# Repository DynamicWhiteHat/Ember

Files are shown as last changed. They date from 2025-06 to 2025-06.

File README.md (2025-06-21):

# Ember
## A Custom Designed 10W Diode Laser Cutter

## IMPORTANT: It is imperative to ensure proper safety when operating, observing, or in the vicinity of a powerful laser. Please ensure you have proper PPE equipment and handle lasers safely. Please see the BOM for a recommended pair of PPE.

### Specifications:

- NEJE E40 10W 24v Diode Laser
- Wireless connectivity powered by the MakerBase DLC32 board
- TS35 touchscreen
- 400x400 mm total area → 360x360 mm cutting area
- 2x endstops for auto homing
- Dual-driven y-axis
- Emergency Stop

### Why I Designed This Project

I wanted to design a low-cost, yet powerful, laser cutter with ample build space. After looking at [this](https://www.youtube.com/watch?v=NyUJvcocJpA) YouTube video, I realized that laser cutters are relatively simple to build. This was also my first time designing something major with moving and press-fit parts in Fusion 360, so it was also a learning experience.
I ensured that I included more than just the necessary elements by adding features such as wireless connectivity and touchscreen access. Nonetheless, this project can still be improved, as it could use more precise 0.9° steppers and lacks an air assist system.
Overall, this was a fun yet demanding project that tested my skills in planning, design, and budgeting, and I think I created a good final product.

### Image Gallery





Rough Wiring: 

Untitled presentation

### BOM
NOTE: Without the AliExpress welcome deal (which only applies to the first product I order), most of these products are cheaper from Amazon, which is why many of them are sourced from there.

Recommended PPE (anything OD 6+): https://www.amazon.com/190nm-490nm-Professional-Protective-Wavelength-Protection/dp/B08R4PMCHR 
| Part | Quantity | Price | Link |
|---|---|---|---|
| Laser | 1 | $134.83 | https://neje.shop/products/e40?variant=40316129378440 |
| DLC32+Screen | 1 |  $47.37 | https://www.aliexpress.us/item/3256804976730248.html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 |
| NEMA17 Stepper | 3 |  $25.99 | https://www.amazon.com/STEPPERONLINE-Stepper-Bipolar-42x42x38mm-Connector/dp/B0B38GHRH8/ |
| Endstop | 1 Pack Of 6 (Cheapest) | $9.99 | https://www.amazon.com/REIFENG-Mechanical-Endstop-Horizontal-Ramps1-4/dp/B07PCN6T6F/ |
| 4x 8mm Shaft | 1 Pack Of 4 |  $16.99 | https://www.amazon.com/inches-Vigorous-Linear-Hardened-Printer/dp/B0CXTX5FZ3/ |
| Bed | 1 |  $35.99 | https://www.amazon.com/UniTak3D-Honeycomb-400x400mm-Dissipation-Protection/dp/B0DHH5XBNH/ |
| LM8UU | 1 Pack Of 10 | $7.65 | https://www.aliexpress.us/item/3256806883965670.html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 |
| 4x 2020 Extrusions + Gussets | 1 Pack Of 4 |  $17.99 | https://amazon.com/Aluminum-Extrusion-European-Standard-Anodized/dp/B0CLGYRKS8/ |
| GT2 Pulley + Belt + Idlers | 1 |  $13.99 | https://www.amazon.com/KeeYees-Timing-Tensioner-Torsion-Printer/dp/B07JKT5BZQ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 |
| E-STOP | 1 | $2.00 | https://www.aliexpress.us/item/2255800895415537.html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 |
| PSU | 1 |  $35.99 | https://www.amazon.com/ALITOVE-100-240V-Converter-Transformer-5-5x2-5mm/dp/B0B17Z1V6B/ |
| TOTAL: | | $348.78 | |

Additional parts (out of pocket cost) [screws](https://www.amazon.com/HanTof-Countersunk-Machine-Wrenches-Threaded/dp/B0B9HWVV61/)

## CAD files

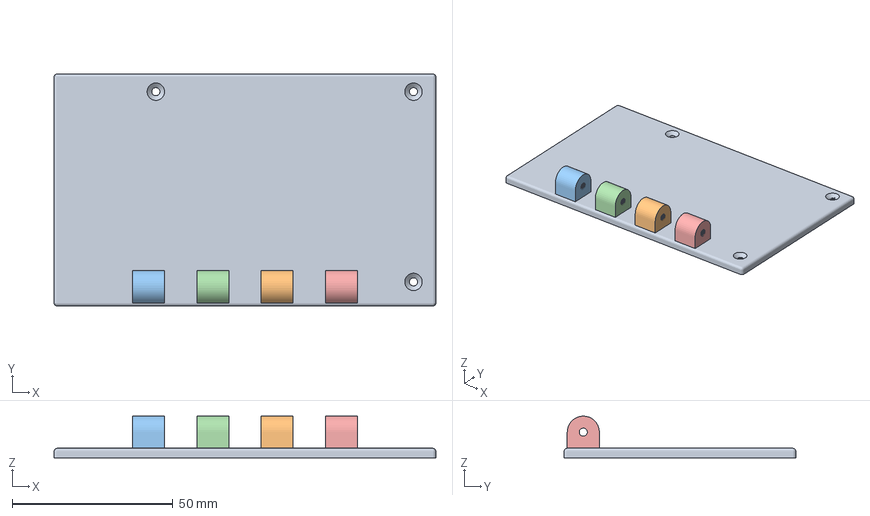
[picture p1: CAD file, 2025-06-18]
CAD/Prints/3MF/MCU/MainTop.3mf
118.9 x 72.2 x 13.0 mm

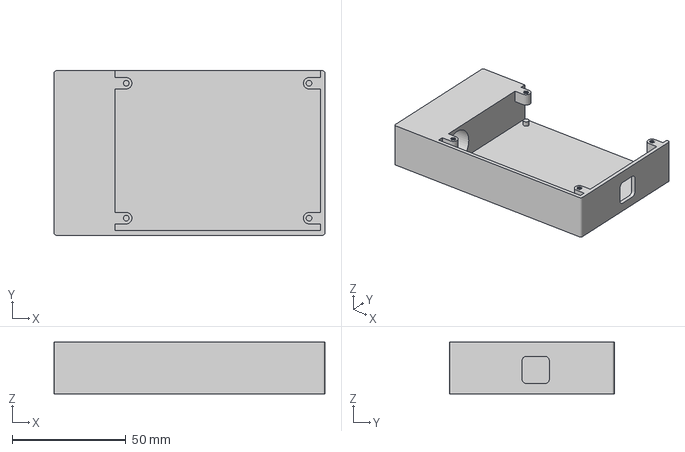
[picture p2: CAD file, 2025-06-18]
CAD/Prints/3MF/MCU/MainBottom.3mf
118.9 x 72.2 x 22.7 mm

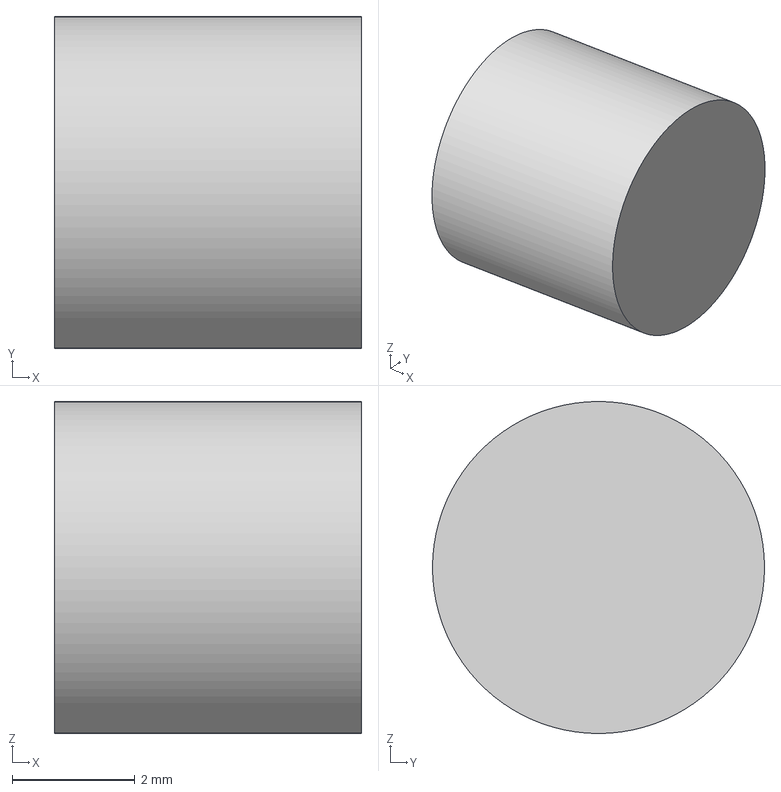
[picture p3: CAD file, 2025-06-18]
CAD/Prints/3MF/Extras/BearingFiller.3mf
5.00 x 5.40 x 5.40 mm

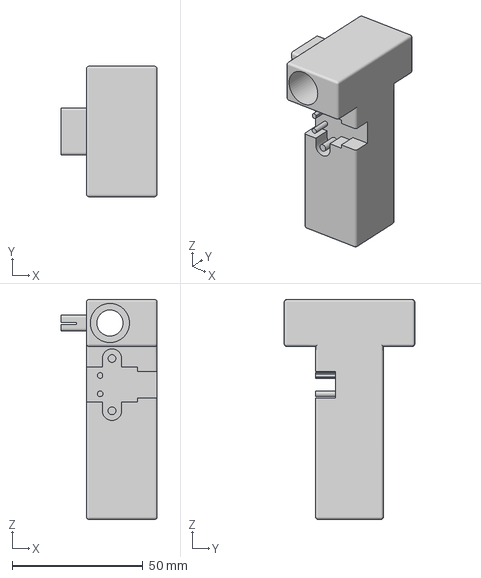
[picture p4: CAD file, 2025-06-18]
CAD/Prints/3MF/Motion/LeftX.3mf
36.9 x 50.0 x 84.2 mm

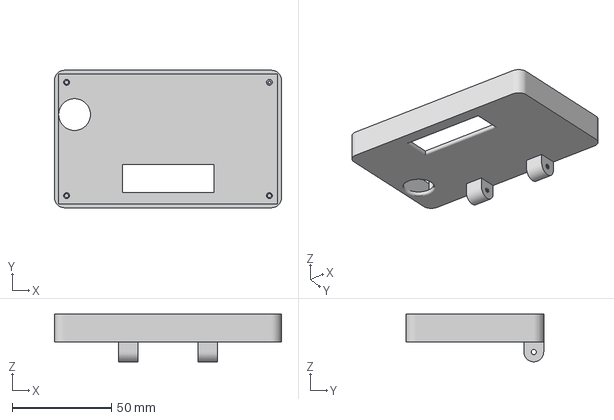
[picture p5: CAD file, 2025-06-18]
CAD/Prints/3MF/Screen/ScreenBottom.3mf
114.2 x 69.2 x 24.0 mm

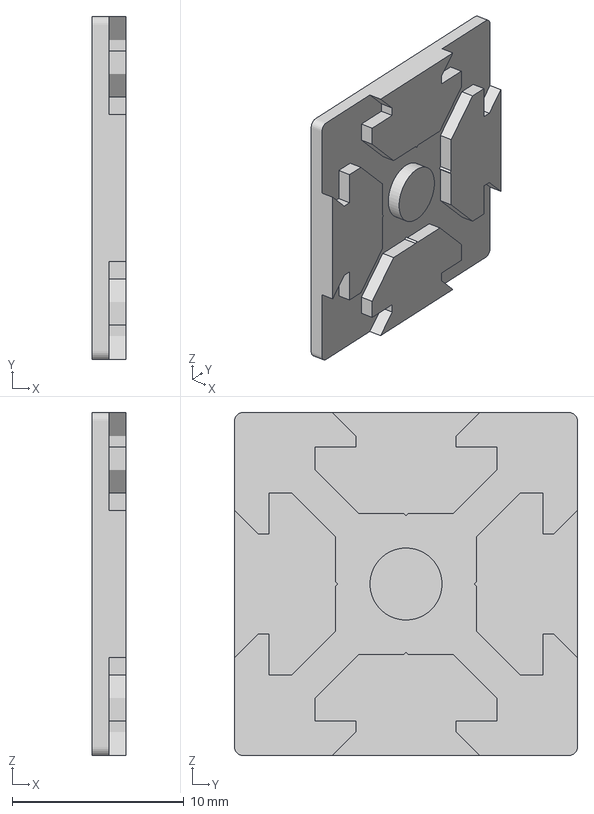
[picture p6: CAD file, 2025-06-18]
CAD/Prints/3MF/Extras/EndCaps2020.3mf
2.00 x 20.0 x 20.0 mm

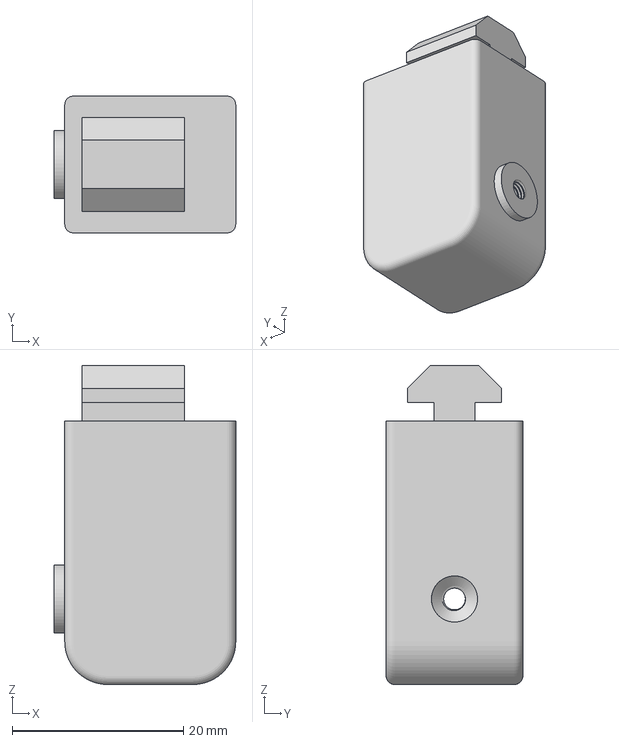
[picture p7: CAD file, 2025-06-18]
CAD/Prints/3MF/Motion/BRightBearing.3mf
21.2 x 16.0 x 37.3 mm

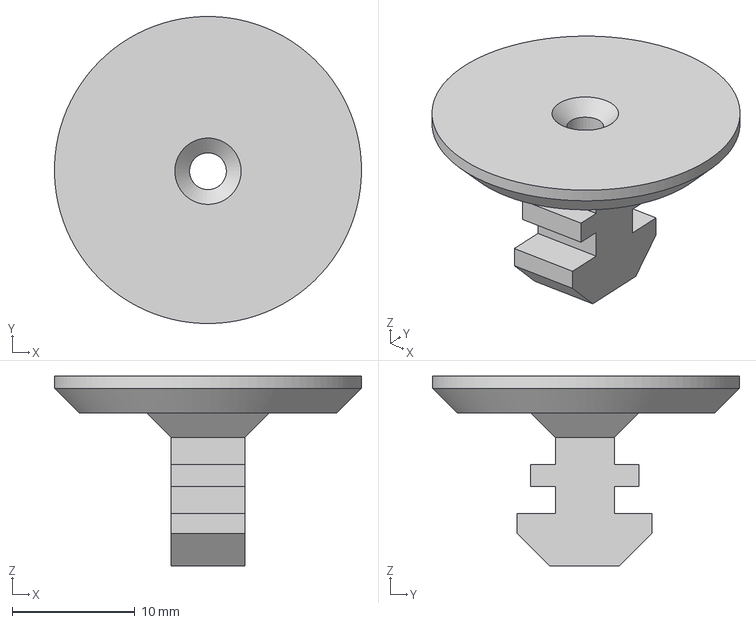
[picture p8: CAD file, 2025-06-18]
CAD/Prints/3MF/Motion/Foot.3mf
25.0 x 25.0 x 15.5 mm

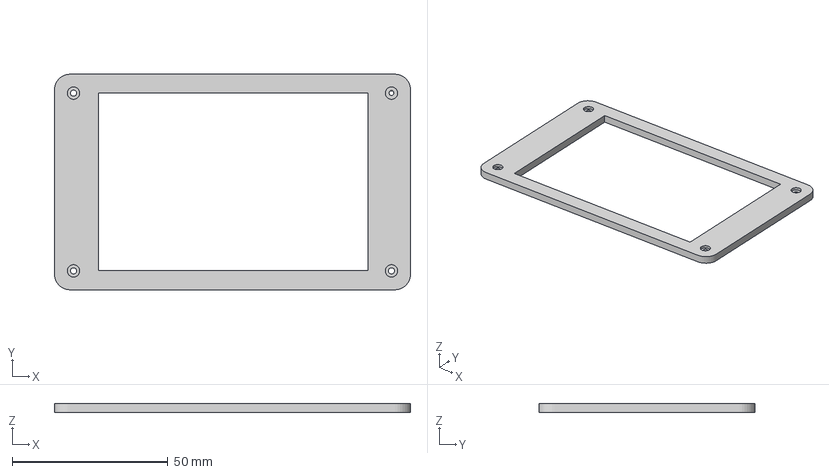
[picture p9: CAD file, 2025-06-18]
CAD/Prints/3MF/Screen/ScreenLid.3mf
114.2 x 69.2 x 2.94 mm

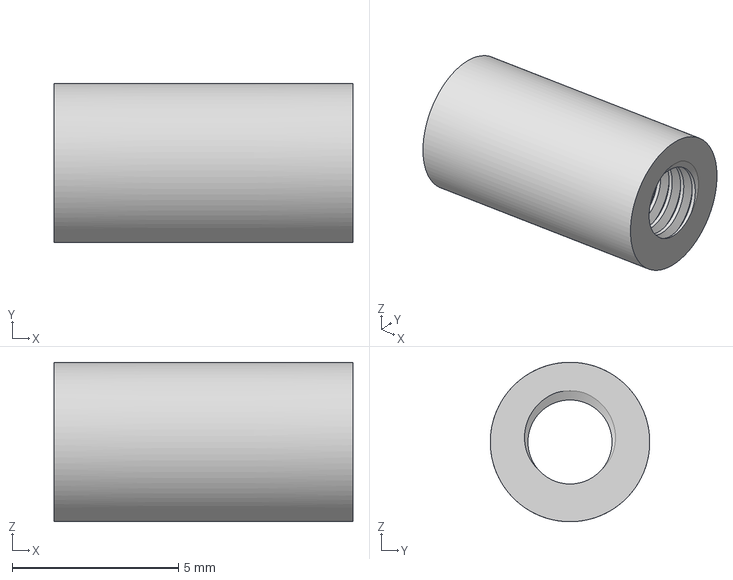
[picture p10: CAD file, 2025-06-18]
CAD/Prints/3MF/Motion/BearingInsertRight.3mf
9.00 x 4.80 x 4.80 mm

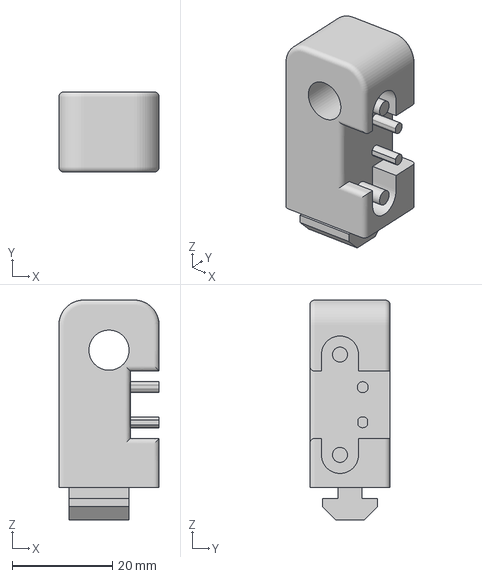
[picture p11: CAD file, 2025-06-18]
CAD/Prints/3MF/Motion/FRight.3mf
20.0 x 16.0 x 43.8 mm

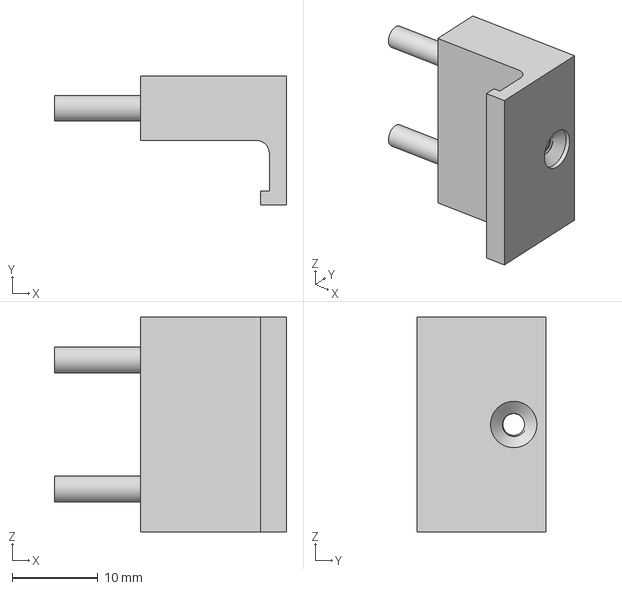
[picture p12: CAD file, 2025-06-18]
CAD/Prints/3MF/Motion/ZHolder1.3mf
27.0 x 15.0 x 25.0 mm

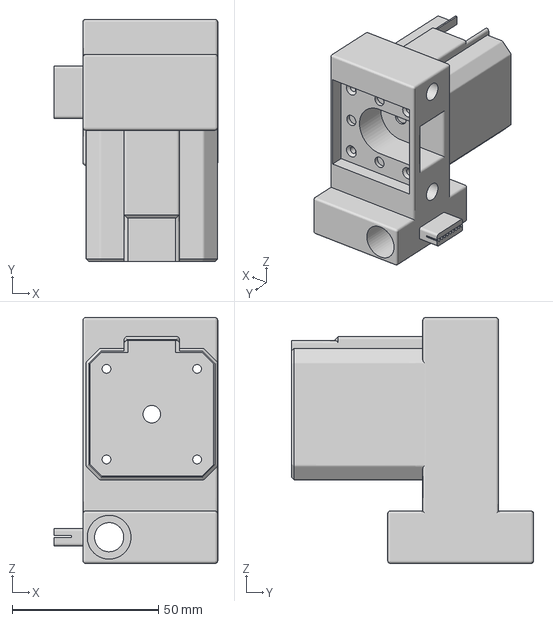
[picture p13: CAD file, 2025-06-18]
CAD/Prints/3MF/Motion/RightX.3mf
56.0 x 83.0 x 84.2 mm

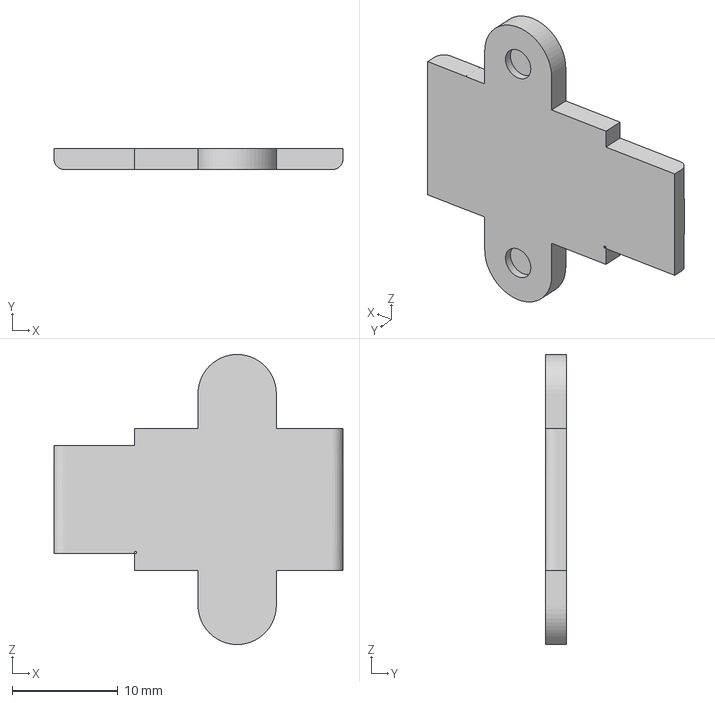
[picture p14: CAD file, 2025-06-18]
CAD/Prints/3MF/Motion/LeftMagnet.3mf
27.3 x 2.00 x 27.4 mm

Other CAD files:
CAD/Prints/3MF/Motion/BLeftBearing.3mf
CAD/Prints/3MF/Motion/BearingInsertLeftX.3mf
CAD/Prints/3MF/Motion/Holder.3mf
CAD/Prints/3MF/Motion/Magnetic.3mf
CAD/Prints/3MF/Motion/BLeft.3mf
CAD/Prints/3MF/Motion/BRight.3mf
CAD/Prints/3MF/Motion/BearingInsertLeft.3mf
CAD/Prints/3MF/Motion/FLeft.3mf
CAD/Prints/3MF/Motion/ZHolder2.3mf
CAD/Prints/3MF/Screen/ScreenScrew.3mf
CAD/Prints/STL/Extras/BearingFiller.stl
CAD/Prints/STL/Extras/EndCaps2020.stl
CAD/Prints/STL/MCU/MainBottom.stl
CAD/Prints/STL/MCU/MainTop.stl
CAD/Prints/STL/Motion/BLeft.stl
CAD/Prints/STL/Motion/BLeftBearing.stl
CAD/Prints/STL/Motion/BRight.stl
CAD/Prints/STL/Motion/BRightBearing.stl
CAD/Prints/STL/Motion/BearingInsertLeft.stl
CAD/Prints/STL/Motion/BearingInsertLeftX.stl
CAD/Prints/STL/Motion/BearingInsertRight.stl
CAD/Prints/STL/Motion/FLeft.stl
CAD/Prints/STL/Motion/FRight.stl
CAD/Prints/STL/Motion/Foot.stl
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

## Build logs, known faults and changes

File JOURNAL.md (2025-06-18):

# Ember
A Custom Built 10w Laser Cutter

---
title: "Ember"
author: "DynamicWhiteHat"
description: "A custom-built $350 10w laser cutter."
created_at: "2025-06-13"
---

# Total Time Spent: 25 Hours

# June 13th: Selected parts and started CAD

I first started off by selecting the laser for my laser cutter. Since I don't have any experience with building or even usign laser cutters, I decided to watch a few videos on the topic. [This](https://www.youtube.com/watch?v=7gnD6F0yBH0&list=PLT2B-jiRa_P4blv69gIPtibwSavtNRHN4&index=2) video was particularly useful in helping me understand the topic.

### Choosing the laser

Initially, I had decided to build a CO2 laser like the one in the video, as it is powerful and not too hard to build. However, after looking at the prices for just the CO2 laser tube, I decided to switch to a cheaper and less powerful diode laser. Most CO2 lasers were costing around $200. At this price point, it would be hard for me to get other parts such as the MCU and the steppers while fitting in the motion system.

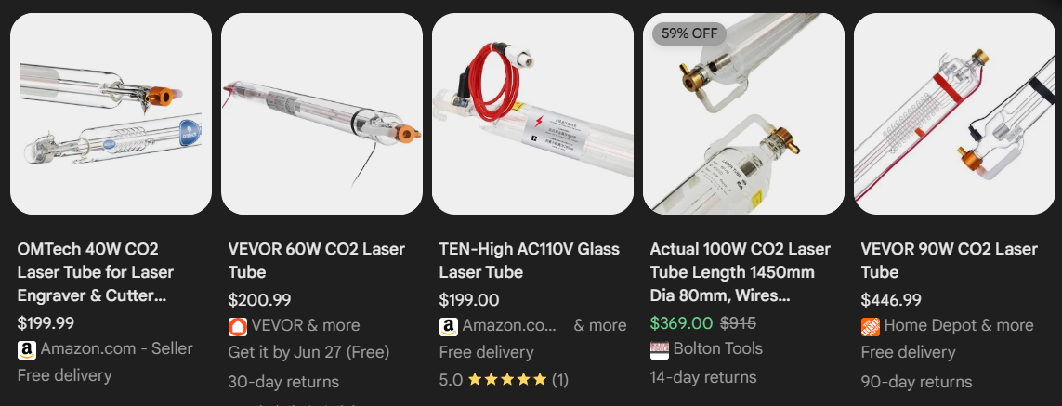
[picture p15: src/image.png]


I decided to switch to buying a 10W diode laser, which is cheaper yet can still cut through many things. Additionally, switching to this cheaper alternative allowed me to fit some additional items in my budget, such as a screen for the MCU. I no longer have to buy mirrors to reflect the CO2 lasers. I narrowed down my selection to these three lasers:

-------------------------------------------------------------------------------------------------------------------
| LaserTree 10W LT-80W-AA-PRO $139 | NEJE E40 $139 | NEJE E30 $99 |
|---|---|---|
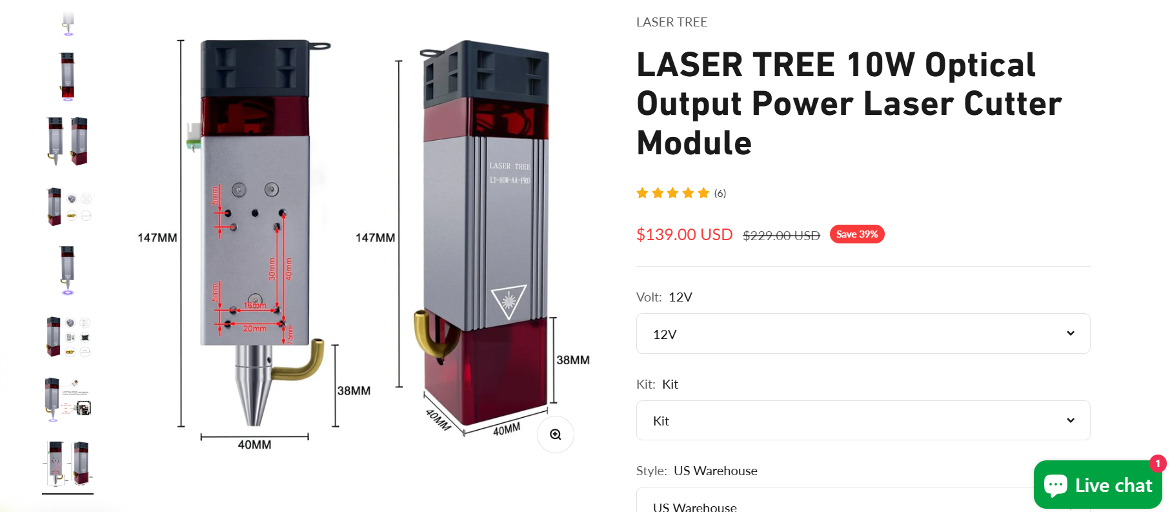
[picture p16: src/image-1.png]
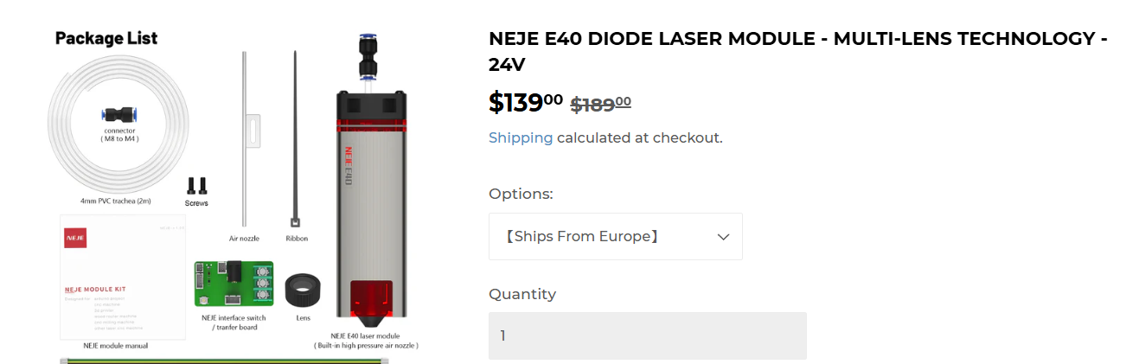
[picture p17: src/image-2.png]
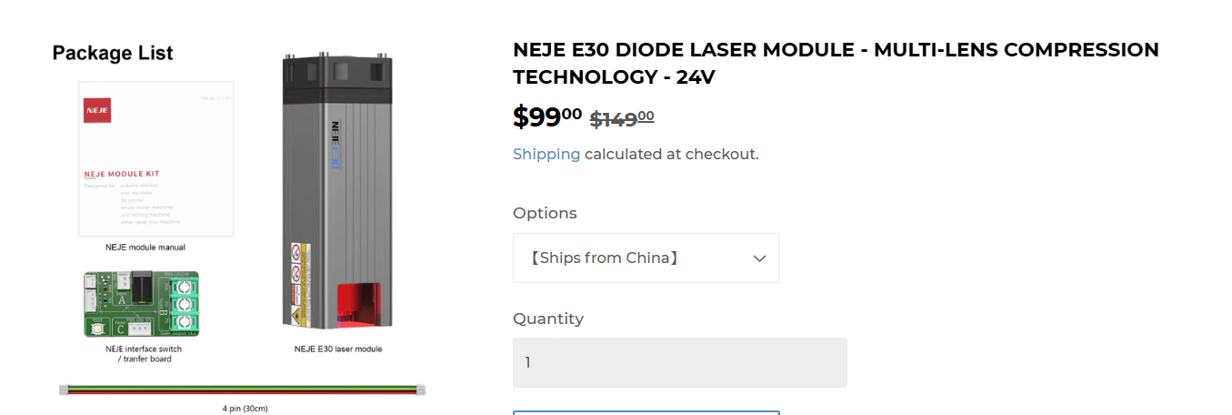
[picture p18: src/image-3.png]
|  |  |  |
-------------------------------------------------------------------------------------------------------------------

After comparing the three, I chose the [LaserTree 10W laser](https://lasertree.com/products/10w-optical-output-power-laser-cutter-module?variant=42608494149783) due to poor reviews of NEJE products that I found online. It also includes some additonal items at the same price point as the NEJE E40. My total cost is now $139.

### Choosing the power supply

I needed to pick a reliable and powerful PSU to make sure that the cutter was getting enough power. I looked online for some recommended ones and settled on [this](https://www.digikey.com/en/products/detail/mean-well-usa-inc/LRS-350-24/7705034) 24v 350W PSU from Mean Well for $32. This brings my total cost up to $171.

### Choosing the MCU

Once again I searched online for some commonly used MCU units. I could either use an Arduino with the CNC shield, which, although it simple to use, doesn't provide many additional features such as wireless connectivity or a display adapter. I also found the MCUs from MakerBase. Their MKS DLC32 caught my eye since it featured an ESP32 allowing wireless connectivity and had the option for a display. I also own a 3D printer that uses a MakerBase MCU, so I have some experience with using their products. I decided to settle on [this](https://www.aliexpress.us/item/3256802997183501.html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) product from the official MakerBase seller on AliExpress. The price for this product is $68, bringing the total price up to $239. The bundle with the display also came with 3 TMC2209 stepper drivers, which meant that I didn't have to buy them separately. 

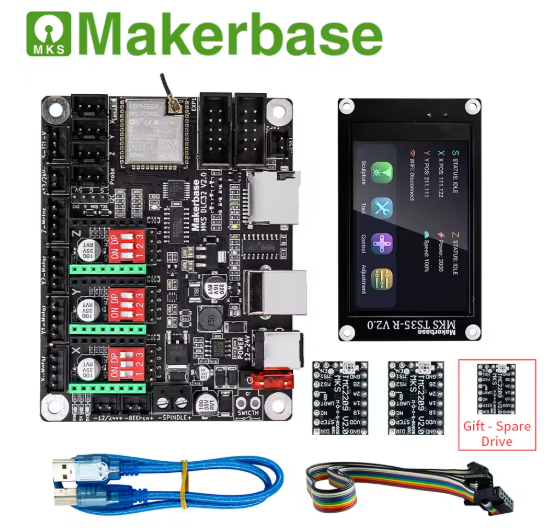
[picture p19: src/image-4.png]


### Choosing the steppers

I have looked into stepper motors before for other projects, so I knew that a good set of quality and powerful stepper motors would be the Nema17 steppers. These motors are widely used in many DIY and commercial products. I found [this](https://www.amazon.com/STEPPERONLINE-Stepper-Bipolar-Connector-compatible/dp/B00PNEQKC0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) Amazon listing for $13, and I needed two of them, so the price for the steppers was $26, bringing the total price up to $265.

### Additional parts

Now that I have the main parts selected out, I decided to look into a few additional parts that add to ease of use. First, I picked out some mechanical endstop switches to make zeroing a breeze. I found [this](https://www.amazon.com/REIFENG-Mechanical-Endstop-Horizontal-Ramps1-4/dp/B07PCN6T6F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) 6 pack on Amazon for $11. I also settled on [this](https://www.amazon.com/APIELE-Momentary-Button-Mushroom-Waterproof/dp/B09KZJ2LF6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) 16mm button for emergency stopping for $8. Finally, I picked out a $36 [aluminum honeycomb bed](https://www.amazon.com/UniTak3D-Honeycomb-400x400mm-Dissipation-Protection/dp/B0DHH5XBNH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) for the laser cutter to cut on. The total for additonal parts is $55, bringing the total to $320.

### CAD

I started doing the CAD and decided to make an enclosed cutting system to prevent eye damage. I started the CAD by importing a few 2020 aluminum T extrusions from McMasterCarr into Fusion and built a box. This was my first time using joints and it was great to see everything fit together perfectly without me having to meticulously move things into position. At the end of this session, I ended up with this outline:

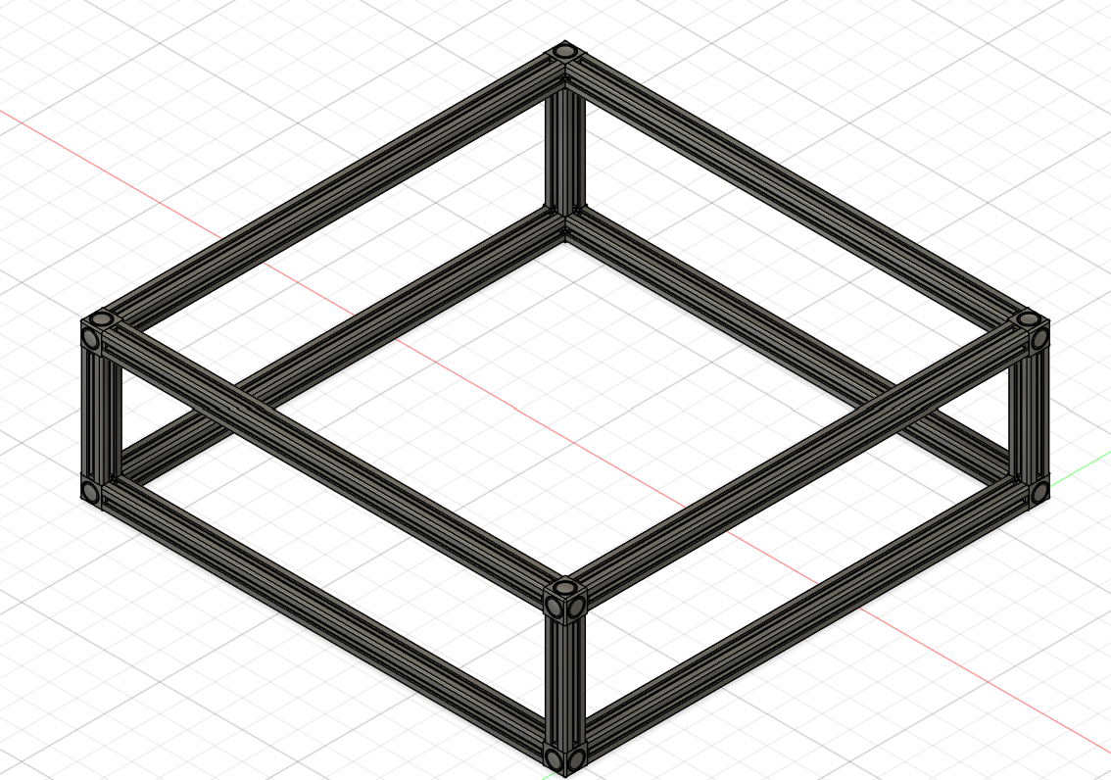
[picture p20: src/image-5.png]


I might have to cut the cost on some parts to be able to fit this design into the $350 budget.

### Total time spent: 5 hours

# June 15th: CAD

I decided to restart my CAD since doing a fully enclosed cutter would most likely exceed the $350 budget. Instead, I opted to do an open design, especially after I sa that the laser module has a laser filter around the beam itself, so it should be safe to run without an enclosure. I found [this](https://www.youtube.com/watch?v=NyUJvcocJpA&t=475s&pp=ygUQZGl5IGxhc2VyIGN1dHRlcg%3D%3D) video online which gave me a good idea on how to start this design. I first created the frame for everything using 2020 aluminum extrusions and closed gusset corner brackets for stability and added some feet.



After that, I tried to create the y-axis, but I just couldn't figure out how to design it. I understood how the mechanics of it worked, but I didn't know where to begin designing it. After looking at some other 3D printed designs online, I found [this](https://www.thingiverse.com/thing:3567976/files) design, which was very helpful. It also had a PDF for how to build it, which allowed me to understand how parts fit each other. After I found this design, I started updating my own design and ended up with this for the y-axis:



Designing this took a while since I forgot to account for the height of the stepper motor, which made me redesign the 8mm rod holders once I started the steppers. This was also my first time using joints to create motion, and I used this to make rotating GT2 belt pulleys.

Finally, I started on the x-axis. The first YouTube video I found placed their rods on the same horizontal axis, which made the overall design shorter. The 2nd design I found had them placed vertically, which made it taller. However, because of the 2nd design's taller x-axis, there was more surface area to attach the laser itself, giving it better stability, so I decided to go with this design. This is my x-axis, which I have to finish.



### Total time spent: 10 hours

# June 16th: Finished CAD

I spent most of the day working on the CAD model. The first thing I did was finish the x-axis. I had to add the stepper motor onto one end of the axis, which made the holder for it very large. One issue I ran into while designing this portion was that there were no M3 screws greater than 20mm available for cheap online to fasten the motor onto the 3D printed part. The workaround I came up with was a magnetic plate that went over top of the screws to hide an indent I made so I could fit shorter screws. That ended up looking like this:

| Plate Off | Plate On |
|---|---|
|  |  |

After that bit, I worked on adding in the GT2 pulley and the idler pulley on the x-axis ends. The right side had the motor on it, so that side had the pulley. The left side of the axis had the idler pulley added to it. Once this was complete, my axis looked like this:



The next thing I had to add was the mount for the laser diode itself. I was able to find a 3D model of the laser on [Thingiverse](https://www.thingiverse.com/thing:6265918/files). I found this model especially interesting since the designer was able to model the laser while preserving many of its details in Tinkercad. I was confused about how the laser head would attach to the axis, but I found an amazon listing for a part that comes with the laser and that cleared everything up. I mounted the laser near the top half of the center, which ended up looking like this:

|  |  |
|---|---|

The only part left to model was the main control board (DLC32) and the touchscreen for it. I imported some 3D models I found on GrabCAD and projected their edges with an offset of 0.2. This let me quickly extrude out a box for the board and screen. I left the back for the board open to allow wires to come through. Once I was done with those two, I added spots for the endstops. This was a bit difficult since I was not able to find an exact 3D model online and the listing had very little information on measurements. I edited a similar model I found and used it to make cavities to put them in. This is my final design:



The only thing left to do is source the parts and find cheaper alternatives for other parts since I know I will go over budget. If I need to reduce a lot of money, I can switch to the $99 laser head, which would give me $50 more to work with.

### Total time spent: 8 hours

## Final Design Addition 6/17/25

I was working on making sure everything fit under $350, and I decided to change to the NEJE E40 instead of the LaserTree since NEJE offers free shipping compared to LaserTree's $35. This required a redesign of the x-axis holder for the laser, which now looks like this:



I also realized while looking for 2020 extrusions that the model I was using in Fusion had smooth inside edges whereas the actual ones had sharp edges. This once again required a redesign of the components that required a tight fit instead of screws to stay in place.

Now that I've finished all that and selected the parts, I think the design of this project is finally complete!

### Time spent: 2 hours

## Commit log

2025-06-18 Update Ember BOM - Sheet1.csv
    [Ember BOM - Sheet1.csv]
2025-06-19 Added STL
    [BLeft.3mf, BLeft.stl, BLeftBearing.3mf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]
